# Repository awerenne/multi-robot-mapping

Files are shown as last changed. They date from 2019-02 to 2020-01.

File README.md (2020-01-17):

# Multi-robot environment mapping 

The goal of this project was to construct two robots, able to map unknown environments as quickly as possible. The considered environments are exclusively composed of straight black lines on a white background, intersecting each other with right angles. The robots being only allowed to move along those black lines during the exploration phase.

The developed solution follows a master-slave architecture. Each robot (slave) follows a black line while keeping track of the travelled distance. Once an intersection detected, the robot stops and sends an information message to the master. The message contains the type of intersection encountered and the travelled distance since the previous intersection. This information is then used by a program (master), running locally on a computer, in order to update its internal representation of the environment (i.e. map). The next instruction (stop, straight, turn left or right, uturn) for the robot is then computed and send back to the rboto. This procedure is repeated until the environment is entirely explored.

<p align="center">
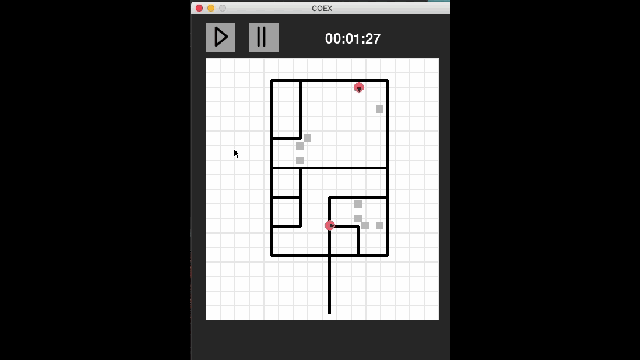
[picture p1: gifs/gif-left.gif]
    &nbsp;&nbsp;&nbsp;
    
</p>

The left-part of the animation above shows a live screen recording of the master constructing the map, corresponding to the robot exploration performed (displayed in the right-part). A video of the complete demonstration can be found [here](https://www.youtube.com/watch?v=w8zaz-Xr6bw&t=6s). The implementation and results are described in the [report](https://awerenne.github.io/files/pp-report.pdf). The different steps of the construction of the robots are documented [here](https://github.com/awerenne/multi-robot-mapping/blob/master/construction/README.md).

## Simulator
Testing the mapping algorithm with the exploration being performed by physical robots would have been time-consuming. Instead, the exploration was simulated on random environments. 

<p align="center">
    
</p>

The algorithm of the master is explained in the [report](report/personal-project.pdf)) (pages 8-11). A simulation can be lauched with <code>python main.py</code> in the folder *code/simulator/*. The flag <code>is_simulation</code> needs to be set to true in the config file.

## Robot
The control of the robot was tested with a simple challenge: following a curved line at a constant speed. To this end, a speed and steering controller were developed (described in the [report](report/personal-project.pdf), pages 20-24). The result is shown in the animation below.

<p align="center">
    
</p>

The robot was then further augmented to loop through a serie of steps during the exploration phase. The high-level view of the main algorithm (serie of steps) is implemented in the file *code/robot/mapping/mapping.ino*, which is based on low-level features implemented in the files located in the folder *code/robot/NewCOEX/*. The acronym COEX stands for cooperative explorer. 

<p align="center">
    
</p>

## Usage
The simulator can be launched as follows:
1. Set the flag <code>is_simulation</code> to True in the config file.
2. Run the command <code>python main.py</code> (in the folder *code/simulator/*).

The physical exploration can be launched as follows:
1. Copy the folder *code/robot/NewCoex* in your Arduino folder, and load it as a library ([how to load a library](https://www.arduino.cc/en/guide/libraries)).
2. Install the library corresponding to the [QTR-X sensors](https://www.pololu.com/docs/0J19/2).
3. Upload the program *code/robot/mapping/mapping.ino* to the micro-controller.
4. Set the flag <code>is_simulation</code> to False in the config file.
5. Check that the ports in the config files are correctly configured with the names of the bluetooth modules.
5. Switch the power of the robots on and calibrate the line sensors.
6. Run the command <code>python main.py</code> (in the folder *code/master/*).

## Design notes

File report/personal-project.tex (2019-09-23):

%\documentclass[12pt]{extarticle}
\documentclass[12pt]{report}
\usepackage[utf8]{inputenc}
\usepackage{cite}
\usepackage[hyperfootnotes=false]{hyperref}
\usepackage{xcolor}
\usepackage{tikz}
\usepackage{mathtools}
\hypersetup{
  colorlinks,
  citecolor=blue,
  linkcolor=red,
  urlcolor=blue}
\usepackage{amsmath}
\usepackage{subcaption}
\usepackage{amssymb}
\usepackage{graphicx}
\usepackage{float}
\usepackage{caption}
\usepackage{hyperref}
%\usepackage[linesnumbered,ruled,boxed,algo2e]{algorithm2e}
\usepackage{algorithm}
\usepackage{algpseudocode}
\usepackage{geometry}
%\usepackage{subfig}
\usepackage{bm}
%\geometry{left=30mm, right=30mm, top=30mm, bottom=30mm}
\geometry{
	paper=a4paper, % Change to letterpaper for US letter
	inner=3cm, % Inner margin
	outer=3.5cm, % Outer margin
	bindingoffset=.5cm, % Binding offset
	top=2.8cm, % Top margin
	bottom=2.8cm, % Bottom margin
	%showframe, % Uncomment to show how the type block is set on the page
}
%\usepackage{subfig}
%\usepackage{mwe} % For dummy images
%\usepackage{capt-of}
\usepackage{tabu}
\captionsetup{
	margin=1.2cm,
	format=hang,
	font=small,
	format=plain,
	labelfont={bf,up},
	textfont={it}}
%\setlength{\footskip}{15mm}
\renewcommand{\thesection}{\arabic{section}}
\parskip 1.5ex % paragraph spacing
%\renewcommand{\baselinestretch}{1.33} % line spacing
\begin{document}
\newcommand{\HRule}{\rule{\linewidth}{0.5mm}} % Defines a new command for the horizontal lines, change thickness here
 
%----------------------------------------------------------------------------------------
%	AUTHOR SECTION
%----------------------------------------------------------------------------------------

\begin{titlepage}
\begin{center}

%\vspace*{.06\textheight}
%{\scshape\LARGE \univname\par}\vspace{1.5cm} % University name
\textsc{\Large Personal Project}\\[0.4cm] % Thesis type

\vspace*{.06\textheight}
\begin{center}
\\[1.2cm] 
\end{center}

\HRule \\[0.4cm] % Horizontal line
{\huge \bfseries Unknown Environment Mapping with multiple robots\par}\vspace{0.4cm} % Thesis title
\HRule \\[1.2cm] % Horizontal line
 
\begin{minipage}[t]{0.4\textwidth}
\begin{flushleft} \large
\emph{Author:}\\
Aurélien \textsc{Werenne }
\end{flushleft}
\end{minipage}
\begin{minipage}[t]{0.4\textwidth}
\begin{flushright} \large
\emph{Advisor:} \\
Bernard \textsc{Boigelot}
\end{flushright}
\end{minipage}\\[2.4cm]

Montefiore Institute\\
Faculty of Applied Sciences\\
University of Liège\\
Liège, Belgium\\[4cm] 

%\begin{center}
%\includegraphics[scale=0.6]{figures/logo-uliege}\\[1.6cm] 
%\end{center}
{\large Academic Year 2018 - 2019}
 
\vfill
\end{center}
\end{titlepage}
\pagenumbering{roman}
\renewcommand{\abstractname}{Foreword}
\begin{abstract}
This work was performed in the context of the optional course \textit{Personal Project} at the University of Liege. The goal of the course is to design and develop a realistic interdisciplinary project from the conceptual to the operational phase. Moreover, the project must be chosen by the student, approved by the advisor and carried out remotely. 

The choice was made to construct two robots cooperating to explore and map an unknown environment rapidly.

To conclude, I would like to express my sincere gratitude to my advisor Prof. Bernard Boigelot at the University of Liège. The door to Prof. Boigelot office was always open whenever I ran into a trouble spot or had a question about my project. He consistently allowed this project to be my own work, but steered me in the right direction whenever he thought I needed it. Thank you.
\end{abstract}
\tableofcontents
\clearpage
\pagenumbering{arabic}
\chapter{Introduction}
%------------------------------------------------
\section{Motivation}
%------------------------------------------------
Constructing a map of environments using robots can be of great interest for rescue teams, especially for environments situated in war zones or affected by natural disasters. In those cases the rapidity component is of particular importance. In an attempt to increase the speed of the exploration process researchers investigated the use of multiple robots \cite{burgard, kurt}.

In this work we decided to develop a simple algorithm for a dual robotic system whose goal is to map an environment like the one shown in Figure \ref{fig:env}. The algorithm was then validated in a self-constructed simulator. Once the results became satisfying, the robots were constructed and tested on physical environments.

\begin{figure}[!h]
\vspace*{4mm}
\centering

\caption{Example of the structure of an environment. The robots start their exploration at the bottom edge. In the physical world, the scale is such that the smallest edge displayed above corresponds to 20 cm.}
\label{fig:env}
\end{figure}

%------------------------------------------------
\section{Problem Statement \& Hypothesis}
%------------------------------------------------
The environments considered are exclusively composed of straight paths\footnote{Also called \textit{edges} and \textit{roads} interchangeably in this work.} intersecting each other with right angles, where the paths are modelled by black lines on a white background (see Fig. \ref{fig:env}). The robots are only allowed to move along the black lines. Furthermore, each robot is equipped with sensors enabling it to i) distinguish the black line from the white background ii) detect and classify an intersection iii) detect the other robot if it is in a very close range.

%------------------------------------------------
\section{Proposed Solution}
%------------------------------------------------
The proposed solution is implemented in the form of a master-slave architecture, where the master will be running locally in a computer and the slaves correspond to the robots (see Figure \ref{fig:master-slave}). The robots move through the environment while incrementing a distance counter until an intersection is encountered. In this case, the robot stops and sends an information message to the master, containing the travelled distance and the type of encountered intersection. The master receives this information, and is used to further construct an internal representation of the map. Next, the master computes the direction the robot needs to move towards to. This instruction is then send to the robot. It is worth noticing that the robot stays at rest during the decision process of the master. The code for this work can be found at \href{https://github.com/Werenne/multi-agent-mapping}{this}\footnote{Url: \url{https://github.com/Werenne/multi-agent-mapping}} repository.

\begin{figure}[!h]
\centering

\caption{Master-slave architecture.}
\label{fig:master-slave}
\end{figure}

The next chapter describes the implementation of the master and simulator. Chapter \ref{chapter-construction} then details the construction/implementation of the physical robot. 

\chapter{Master}\label{chapter-master}

%------------------------------------------------
\section{Random environment generation}
%------------------------------------------------
The structure of the environments on which our system is tested (in the simulator and physical world) is generated randomly. The algorithm for this task had to be written from scratch since no existent one could be found. The procedure is composed of three sequential steps,
\begin{enumerate}
\item \textit{Initialization}: initialize the set of edges as shown in Figure \ref{fig:gener-a}.
\item \textit{Destruction}: remove randomly 80\%\footnote{Determined arbitrary by experimenting.} of the interior edges.
\item \textit{Fixing}: adds an edge randomly on nodes disconnected from the rest of the graph (relative to the \textit{root node}\footnote{The root node refers to the node at the bottom, and corresponds also to the starting point of the robots.}). This process is repeated until all remaining nodes can be accessed from the \textit{root node}.
\end{enumerate}

\begin{figure}[!h]
\centering
\begin{subfigure}{.3\textwidth}
  \centering
  
  \caption{Initialization}
  \label{fig:gener-a}
\end{subfigure}%
\begin{subfigure}{.3\textwidth}
  \centering
  
  \caption{Destruction}
\end{subfigure}
\begin{subfigure}{.3\textwidth}
  \centering
  
  \caption{Fixing}
\end{subfigure}
\caption{Resulting environments of three steps of the generation.}
\label{fig:gener}
\end{figure}

%------------------------------------------------
\section{Simulator}
%------------------------------------------------
It would be costly in time to design, debug and evaluate the performance of the master algorithm if ran in combination with the physical robots. Thus, a simulator was constructed emulating environment and robots. In particular, the simulated robots are constrained to follow edges in the environment, with their sensory inputs limited to a one-step lookahead in the front, left, and right directions. Each robot increments its distance and once they encounter an intersection, an information message is send to the master.

%------------------------------------------------
\section{Communication protocol}
%------------------------------------------------
Messages are of the following form: $<$\textit{identifier}, \textit{sequence number}, \textit{message}$>$. The \textit{message} part corresponds to \textit{information} (type intersection \& distance) if the sender is a robot, or to an \textit{instruction} if it comes from the master. The \textit{identifier} is used to enable the master to distinguish robots, but also to prevent communication between the robots. Lastly, the \textit{sequence number} permits to trigger a recovery mechanism for unreceived messages and to ignore redundant messages. Delimiters ($<$, $>$) are used to verify that the entire message is received.

%------------------------------------------------
\section{Graphical User Interface}
%------------------------------------------------
Simulations are visualized in a Graphical User Interface (GUI), which was made with the framework \texttt{PyGame}\footnote{More information about the \texttt{Pygame} can be found \href{www.pygame.org}{here}.}. The GUI enables us, on the one hand to visualize the internal map representation of the master, and on the other hand the groundtruth environment and robots (see Figure \ref{fig:gui}). In order to keep the simulations smooth, the master, simulator and GUI are executed as separate threads. Let us emphasize that the same GUI is used for the physical robot exploration, but obviously does not display the groundtruth since it is not known \textit{a priori}. 

\begin{figure}[!h]
\centering

\caption{A snapshot of the Graphical User Interface (grey lines correspond to the groundtruth, black lines to the current internal map representation, coloured circles to the robots).}
\label{fig:gui}
\end{figure}

%------------------------------------------------
\section{Architecture \& Decision Algorithm}
%------------------------------------------------
\subsection*{Architecture}
The architecture of the master is composed of three main classes: \texttt{map}, \texttt{messenger} and \texttt{master}. When a message is send by a robot, it is first received, parsed and checked by the \texttt{messenger}. The information is then passed to the \texttt{map}, which updates the internal representation of the environment and the corresponding robot pose (position and orientation). Finally, the \texttt{master} computes and sends the optimal direction that must be taken by the robot.

\subsection*{Decision Algorithm}
A robot arriving at an intersection sends an information, and waits for a response containing the new instruction. This instruction is determined by the decision algorithm of the master and is described in the next paragraph. Beforehand, the concept of \textit{frontier}, although commonly used, must be defined: a frontier is referred to as an intersection with at least one unexplored edge.

The decision algorithm distinguishes three cases when a robot arrives at an intersection. In the first case, the intersection is a frontier, and the new direction is simply chosen by applying the left-hand-rule on the unexplored edges. In the second case, the intersection is not a frontier and there are are no remaining frontiers in the current map. The master concludes that the exploration is completed and the robots are send back to their initial position (root note). In the last case the intersection is not a frontier, however, at least one frontier is still remaining elsewhere in the current map. The robot is then assigned to a frontier, which is the one with the minimum Manhattan distance to the current position of the robot. Once the frontier assigned, the master computes the path to take for the robot via the $\text{A}^*$ algorithm\footnote{The Dijkstra algorithm improved with the heuristic that a path to a goal is always greater or equal to the Manhattan distance to that goal. This permits to avoid unnecessary computations. This heuristic is valid since all the angles are right.}. The robot moves towards the assigned frontier following the determined path. However, the path is recomputed at each intersection since the explored environment expands, and thus new optimal paths could potentially appear.
 
Simulations showed that using two robots with the aforementioned algorithm increased the rapidity by 61\% compared to only using one robot. Although these results may seem sufficient, four problems were observed during the simulations. These problems are described below along with a proposed solution. 

\subsection*{Avoiding robot encounters}
Since rapidity is the main objective, caution must be taken to avoid robot encounters as much as possible. Indeed, the recovery process (described below) would lead to a loss of time. The method applied to avoid encounters is a masking of the neighbouring edges (infinite weights in $\text{A}^*$) in the map around the other robot during the decision algorithm. Two cases are further distinguished. First, if the other robot is on an intersection, the neighbourhood is defined as the set of edges directly connected to that intersection. Secondly, if the other robot is moving on an edge, the neighbourhood corresponds to the neighbourhood of the next intersection the other robot will encounter. 

\subsection*{Handling robot encounters}
Masking the neighbourhood will not guarantee to entirely avoid robot encounters. For example, two robots moving from opposite sides on an unexplored edge cannot be predicted. If such an encounter occurs, one of the two robots is send out of reach, such that the second robot ucan compute a new path and move forward.

\subsection*{Updating assigned frontiers}
During the time a robot moves towards its assigned frontier, the other robot could potentially have already explore it, coming from another side of the frontier. This issue is solved by checking for each newly explored frontier if it has been assigned.

\subsection*{Cooperative strategy}
An attempt is made to induce a cooperative behaviour. We suggest that the exploration may be more efficient if the robots are forced, to a certain degree, to explore separate distant regions. To do this, the cost function deciding which frontier to assign is adapted as follows:
\begin{equation}
\text{cost}(\text{frontier}) = D(\text{current}, \text{frontier}) - \lambda D(\text{frontier}, \text{other robot})
\end{equation}
where the function $D$ represents the manhattan distance between two points, and $\lambda$ is the importance parameter controlling the trade-off between the two terms. Thus, the first term implies to choose the most nearby frontier, whereas the second term induces the robot to chose the frontier which will be the most distant form the other robot.

Different values of $\lambda$ are tested, Figure \ref{fig:coop} shows the mean (mean on 20 explorations) elapsed time\footnote{The elapsed time rescaled by the covered length of the corresponding environment.} of the explorations. The optimal trade-off seems to be for $\lambda = 0.875$.
\begin{figure}[!h]
\centering

\caption{Mean elapsed time for different $\lambda$'s.}
\label{fig:coop}
\end{figure}

%------------------------------------------------
%------------------------------------------------
%------------------------------------------------
%\part{Robot}
%------------------------------------------------
%------------------------------------------------
%------------------------------------------------

\chapter{Robot}\label{chapter-construction}
The first part of this chapter (Section \ref{sec:components} and \ref{sec:phys-constru}) discusses the physical aspects of the robot , id est its components and how these are assembled. The second part then describes the software and control aspect.

%------------------------------------------------
\section{Components \& Functions}\label{sec:components}
%------------------------------------------------
We identified seven different requirements the robots needs to fulfil. They must be able to 
\begin{itemize}
\item perform basic computations.
\item move and rotate.
\item localize black lines on white background.
\item avoid collisions with the other robot.
\item measure the travelled distance.
\item communicate with the master.
\item supply power to its components.
\end{itemize}

\subsection*{Computational unit}
The \texttt{Arduino Nano} is used as the micro-controller. The main advantages being its simplicity of use and relatively small dimensions. On the other hand, the \texttt{Arduino Nano} only contains 14 digital pins and 8 analog pins, where some capabilities (e.g. interrupt, PWM) are only available on a subset of these pins. As a consequence, the connectivity was a puzzle-work and the final result is shown in Figure \ref{fig:electric-diagram}.

\subsection*{Line localization}
Straightforwardly, in order to perform efficient line-following it is important to be able to localize the line with respect to the center of the robot. This is done using an infra-red (IR) reflectance sensor, composed of an infra-red transmitter and a photo-diode receptor. The idea being that the reflectivity of infra-red light varies with the color and distance of the reflecting surface. In particular, the transmitter emits an infra-red beam onto a surface, which reflects the beam back at the diode. For a light-coloured surface (e.g., white background), the intensity of the reflected signal will be high, resulting in a flow of current in the diode. On the contrary, if it is dark-coloured (e.g., black line), then the intensity of the reflected signal will be low, resulting in a blocking diode. Placing an array of those sensors side-by-side, enables the robot to localize the black line. 

Instead of constructing such an array from separate sensors, we use the \texttt{QTRX-MD-06A Reflectance Sensor Array}, consisting of six IR sensors (see Figure \ref{photo-bottom} in Appendix \ref{chap-construction}). In addition, it comes with high-level interface permitting the robot to directly obtain a continuous value for the position of the line (0 if line at left extremity, 5000 if line at right extremity), which is a significant advantage since it improves the smoothness of the control system (see Section \ref{sec:line-control}). 

From this value we will the \textit{error line} is computed, defined as the deviation from the center of the robot. Figure \ref{fig:exp-qtr-flow} shows the error for a manually moving black line. As can be seen, the measures do not contain significant noise, due to under-the-hood pre-processing steps of the \texttt{QTRX} sensor. Despite this, it was found experimentally that shadow differences in luminous environments could affect the performance. To solve this issue, a shield in carton was constructed and placed around the sensor (see Figure \ref{photo-bottom}).
\begin{figure}[!h]
\centering

\caption{Experiment where a black line is moved back-and-forth between the left and right side of the robot.}
\label{fig:exp-qtr-flow}
\end{figure}

\subsection*{Obstacle detection}
Since multiple robots are moving in the environment, collisions could occur. To avoid this, a \texttt{Sharp} sensor is placed in front of the robot to detect its peers. A Sharp sensor is also an infra-red sensor but with an additional feature, it measures the distance to an object and returns a corresponding analog value. In our use-case, the desired behaviour is to trigger a signal quickly for an object in a range close to collision. In order to do this, the \texttt{Sharp GP2Y0D805Z0F} was chosen, detecting objects in a range 0.5-5 cm interval, and has a very responsive detection time.

It is recommended to add a bypass capacitor because the sensor draws current in large and short bursts. A bypass capacitor is a low-pass filter placed across the power and ground close to the sensor, to diminish the possible interferences resulting from these bursts.

\subsection*{Moving}
The robot is designed as a differentially steered two-wheel. Differential in the sense that both wheels can have different rates of rotations but unlike a differential gearing system as in automobiles, a differentially steered system will have both wheels powered. In other words, to go to the left (resp. right) the speed of the right (resp. left) motor is increased. Additionally, a free rotating wheel is placed at the front of the robot to keep the body in balance. The wheels are powered by brushed DC gearmotors with a 150:1 ratio (see Figure \ref{photo-bottom} in Appendix \ref{chap-construction}), controlled by sending a special form a digital signal, namely a pulse width modulation (PWM). The higher the absolute value of the PWM, the faster the revolutions of the motor are (a negative PWM corresponding to rotations in the opposite direction). Lastly, a dual H-bridge \texttt{L298n} is used in order to decouple the power supply to the motors and the arduino. 

\subsection*{Distance Measurement}
The robot computes the travelled distance in incremental steps by multiplying speed and time, at short regular intervals. For this purpose, two quadrature encoders are soldered to the motors in order to measure the speed. The idea is that the rotating DC motors induce a hall effect in the encoders at each rotation. The used encoders trigger six counts per revolution. The number of revolutions of the left and right motor, are denoted respectively $n_L$ and $n_R$. The angular velocity of the left wheel can be computed as
\begin{equation}
w_L = 2\pi f_L
\qquad\text{with}\qquad	
f_L = \frac{n_L}{6\, G_b \, \Delta{t} }
\end{equation}
with $G_b$ the gearbox ratio, $f_L$ the rotation frequency and $\Delta{t}$ the elapsed time. The angular velocity of the right wheel is computed in an analogous manner. The robot being modelled as differentially steered two-wheel, we obtain the speed of the robot as
\begin{equation}
v = \frac{v_L + v_R}{2} = \frac{R(w_L + w_R)}{2}
\end{equation}

with $R$ the radius of each wheel. Thus, the travelled distance is written,
\begin{align*}
\Delta{x} &= v\Delta{t}\\
&= \frac{\pi R}{6 G_b}(n_L + n_R)
\end{align*}
Several factors are not taken into account in this computation such as acceleration, noise in the measurements and the fact that the robot experiences small deviations during the line-following process. With this in mind, the computed distance is discretized in sufficiently large intervals (5 cm) to be considered an entirely error-free measure of the travelled edge length's. Since the counts of the encoders must occur independently of the program flow, interrupt routines were used.

\subsection*{Communication}
Communication with the master is performed via a bluetooth module \texttt{HC-06}, which is adapted for establishing short range wireless data communication between two systems. Notably, a voltage divider was added to the circuit because of the difference between the logic level voltage of the Arduino ($0-5$ Volt) and the bleutooth module ($0-3.3$ Volt) (see Figure \ref{fig:electric-diagram}):

\begin{align*} 
V_{arduino} &=  \frac{R_4}{R_3+R_4}V_{bleutooth} \\[0.4cm]
 &=  \frac{2.2}{3.2}V_{bleutooth}
\end{align*}

\subsection*{Power supply}
Most components have a low current consumption, and no high-performance speed was required. Thus, a rechargeable NiMH Battery of 7.2 Volts with a capacity of 900 mAh seemed sufficient.

%------------------------------------------------
\section{Physical construction}\label{sec:phys-constru}
%------------------------------------------------
The robot is constructed following the steps described below:
\begin{enumerate}
\item A chassis is cut from wood and used as a base. Additionally, four small pillars are pasted at the corners (see Figure \ref{photo-chassis} in Appendix \ref{chap-construction}).
\item The H-bridge is screwed on the chassis.
\item A breadboard is pasted on the pillars.
\item The micro-controller is soldered into header pins which are then fixed in the breadboard.
\item The encoders are soldered to the motors, and the latter are then fixed on the bottom of the chassis.
\item The wheels are placed on the shafts of the motors, and the omni-wheel is placed under the chassis, at the front.
\item The Sharp and QTR sensor along with its shields are fixed at their desired place.
\item Wiring all the components (see Figure \ref{fig:electric-diagram}).
\item Connect to the power via a soldered switch.
\end{enumerate}

\clearpage
\vfill
\begin{figure}[!h]
\centering

\caption{Electric diagram of the robot}
\label{fig:electric-diagram}
\end{figure}
\vfill
\clearpage

\section{High-level algorithm}\label{sec:high-algo}
The main steps of the robot's algorithm are detailed below. As can be observed, the robot executes mostly physical operations whereas the Master does all the 'smart' stuff.

\begin{algorithm}
    \caption{High-level view algorithm robot}
    \label{euclid}
    \begin{algorithmic}[1] % The number tells where the line numbering should start
    		\Procedure{main}{} 
    			\State active $\gets$ False
    			\State distance $\gets$ 0
			 \While{True}
			 	\If{\Call{checkMessage}{}}
					\State instruction $\gets$ \Call{readMessage}{}  
					\If{instruction $== 0$}
						\State \Call{stopMotors}{}
						\State active $\gets$ False
					\Else
						\State \Call{execInstruction}{instruction} \Comment{turn left, turn right, uturn}
						\State active $\gets$ True
					\EndIf
				\EndIf
				\If{active}
					\State \Call{followLine}{}
					\State distance $\gets$ \Call{measureDistance}{} + distance
					\If{\Call{isIntersection}{}} \Comment{see subsection below}
						\State type $\gets$ \Call{classifyIntersection}{} \Comment{see subsection below}
						\State \Call{forwardAlign}{} \Comment{see subsection below}
						\State \Call{send}{distance, type} \Comment{to Master}
						\State active $\gets$ False
					\EndIf
				\EndIf
				\State \Call{wait}{20} \Comment{milliseconds}
			 \EndWhile        		
        \EndProcedure
    \end{algorithmic}
\end{algorithm}

\subsection*{Intersection detection \& classification}
An anomaly is triggered when a black line is detected at one of the extremities of the \texttt{QTR} sensor. To distinguish noise, the robot continues its execution and checks if the same anomaly pattern occurs consecutively. If this is the case, the anomaly is finally viewed as an intersection. Whenever an intersection is detected, it continues its movement for a few inches in order to classify its type as given by Figure \ref{fig:types}.

\begin{figure}[!h]
\centering

\caption{Different types of intersections.)}
\label{fig:types}
\end{figure}

\subsection*{Forward align}
Since the robot rotates around its central point between the wheels, the robot first aligns the wheels with the detected intersection. This permits the robot to remain nicely aligned after a turn, and thus avoids large initial deviations in the line-following. In other words, once an intersection detected, the robot moves forward for a distance equivalent to its own length. As there may be no black line in front, the robot moves without the follow-line procedure, and instead controls the speed of the motors to be equal, in order to move in a straight line.

\section{Architecture}\label{sec:archi}
Figure \ref{fig:architecture} shows the architecture of the implementation in the micro-controller. The \textit{main} corresponds to the algorithm above. The \textit{COEX} class refers to the high-level features related to the cooperative exploration, which is based on low-level features. The advantages offered by this modularity are two-fold: it makes the debugging easier, and the low-level features can be re-used for a different purpose.

A particular problem observed experimentally was that the sensors and actuators obtained optimal performance levels at different frequencies. The implementation assigns a frequency object to each component to solve this issue.

\begin{figure}[!h]
\centering

\caption{Architecture of the code of the robot.}
\label{fig:architecture}
\end{figure}

%------------------------------------------------
\section{Control}
%------------------------------------------------
\subsection*{Line Following \& Speed Control}\label{sec:line-control}
As an amateur roboticist I naively thought that the robot would go straight if the signals (PWM) send to the left and right motor were equal. Figure \ref{fig:probs-control} shows the result of an experiment were the same PWM signal is send to both motors and their respective speeds are measured with the encoders. A varying difference between the two motors can clearly be noted. Moreover, we also observe that this relationship varies as the power supply discharges. With this in  mind a speed controller was developed in addition to a line-following controller. The two controllers take the form of a PID (with anti-windup) and are combined as shown in Figure \ref{fig:control-base}. Straightforwardly, the error of the speed controller is the \textit{target speed}\footnote{For the demo we fix the target speed to 8 centimeter per second.} $v^*$ minus the \textit{measured speed} $v$. On the other hand, the error of the direction controller is given by the so-called \textit{error line}, $x^*-x$ (previously discussed in Section \ref{sec:components}). The computed PWM values are denoted $u_L$ and $u_R$ for the left and right motor.
\begin{figure}[!h]
  \centering
  
\caption{Variations of speed between the motors}
\label{fig:probs-control}
\end{figure}

The tuning of the parameters of the speed controller is done with respect to a target speed varying as in Figure \ref{fig:tuning}. Notice that the measured speed in this Figure is the one obtained using the tuned parameters. The speed controller seems to work but there is still some room for improvements. However, the results were sufficient for our purpose and thus no further tuning was applied. 
\begin{figure}[!h]
\centering
\begin{subfigure}{.5\textwidth}
  \centering
  
  \caption{multiple cycles}
\end{subfigure}%
\begin{subfigure}{.5\textwidth}
  \centering
  
  \caption{average trend with bandwith representing the variance}
\end{subfigure}
\caption{Experiment speed control with a varying target speed}
\label{fig:tuning}
\end{figure}

To adjust the parameters of the direction controller, the robot was placed on a parcours formed by curved black lines. The heuristic used for tuning was to double the $K_p$ parameter until oscillations occurred, then half it back one time and start to tune the other parameters. Once this was done, the target speed was increased by a small increment and the process repeated (until the desired behaviour). 

By experimenting, several improvements were developed as can be viewed in the block diagram of Figure \ref{fig:control-base}. Indeed, the first observation to make is that there are a lot starts/stops during the exploration, which causes instabilities. It was suspected that this was due to a high current drainage by the motors for a sudden acceleration. The proposed solution implements a smoother acceleration profile\footnote{See Appendix \ref{chap-extra}.}. For a desired target speed to attain in a specific time interval, an intermediate value is computed, namely the \textit{progress speed} The progress speed follows an acceleration in trapezoidal form, permitting the robots to perform a slower start. 

Another challenge is that there can be a misalignment between the black line and the center of the robot after a turn. As a result, a \textit{derivative kick}\footnote{A derivative kick refers to a very large derivative as a consequence of a significant error. As large corrections are undesired, a common approach is to derive the measurements instead (already our case by default since setpoint remains unchanged) and to fix initial derivation to zero.} can occur, which was solved by fixing the initial derivation to zero. A second consequence of the misalignment is that in combination with the smooth acceleration, the correction at start from the direction controller is potentially significantly large with respect to the correction of the speed controller. This issue was solved by having a dynamic setpoint weighting, such that the direction correction is weighted with an hyperbolic tangent function converging rapidly with time to unity. 

\subsection*{Turning}
The COEX-1 is modelled as a two-wheel robot (see figure below). By integrating the angular velocity under the assumption that $v_R = -v_L$, rotational displacement can be deduced
\begin{equation}\label{eq:theta-turn}
\theta(t) = \frac{2vt}{b} + \theta_0
\end{equation}
\begin{figure}[hbtp]
\centering

\caption{Rotation of COEX-1}
\label{fig:model-turn}
\end{figure}

In order to rotate in a specific direction, a naive approach was first tested: rotating at a given speed and duration to obtain the desired angle using Equation \ref{eq:theta-turn}. The results were not catastrophic, but a significant variance was observed, going from a few degrees to a few dozens. This is not acceptable as our goal is to have the center of the robot aligned as closely as possible to the black line. 

A second approach tested, was to use \texttt{QTR} sensors to detect when the line was in the middle and at that instant, to stop the robot. Notice that if the the robot needs to turn 180 degrees but if edges are at his sides (90 degrees), the robot will stop to soon. To this end, the robot was first rotated with an angle of 130 degrees (using the method of the previous paragraph) and then continued with the \texttt{QTR} solution until the robot is aligned. An improvement was observed, however, the robot always stopped a little too late due to drift of the wheels with the surface and a lack of response time from the sensors/actuators.

Ideally, the robot would decrease its rotation speed when approaching the line and sufficiently slow to stop and be aligned perfectly. The implemented solution uses a simple controller so that the speed is decreased with respect to the error line measured. The deceleration was triggered from the moment the black line was in the range of the sensor (i.e., at one of its extremities).

\newpage
\null
\vfill
\begin{figure}[!h]
\centering

\caption{Schematic diagram of the control system (with anti-windup).}
\label{fig:control-base}
\end{figure}
\vfill
\begin{figure}[!h]
\centering

\caption{Schematic diagram of the improved control system (with anti-windup).}
\label{fig:control-base}
\end{figure}
\clearpage
\newpage

%------------------------------------------------
%------------------------------------------------
%------------------------------------------------
%\part{Result}
%------------------------------------------------
%------------------------------------------------
%------------------------------------------------

\chapter{Conclusion}\label{conclusion}
The algorithm of the master that was developed in simulation, showed satisfying results. We verified an improvement from using two robots instead of one. In addition, a slight performance gain was illustrated by inducing a simple cooperative behaviour, enforcing the robots to explore distant regions to a certain degree.

Constructing and implementing the physical robot to be robust and fast was challenging. Nevertheless, an efficient error-free mapping system with one robot could be demonstrated.

Finally, two robots were used to map a physical environment. No entirely error-free solution was found as collisions could not always be avoided for certain angles and speeds.

%------------------------------------------------
%------------------------------------------------
\newpage
\appendix
\chapter{Smooth acceleration}\label{chap-extra}
The default acceleration profile is uniform (see Figure \ref{fig:a}). The update of the progress speed is as follows
\begin{align*}
&v_{n+1} \leftarrow v_n + A \, \Delta t_{n:n+1}\\
&\text{with}\,\ A = \frac{v_{target}}{T}
\end{align*}
For a smoother transition, the robot accelerates following the trapezoidal profile as in Fig.\ref{fig:b}. As we want the robot to achieve the target speed in the same amount of time $T$. This constraint is developed,
\begin{align*}
&\Leftrightarrow \int_{0}^{T}a(t) =  \int_{0}^{T}a'(t) \\
&\Leftrightarrow A\,T = \underbrace{d\,B}_{triangles} + \underbrace{(T - 2d)B}_{rectangle}
\end{align*}
\begin{figure}[!h]
\centering
\begin{subfigure}{.5\textwidth}
  \centering
  
  \caption{uniform}
  \label{fig:a}
\end{subfigure}%
\begin{subfigure}{.5\textwidth}
  \centering
  
  \caption{trapezoidal}
  \label{fig:b}
\end{subfigure}
\caption{Acceleration profiles.}
\label{fig:ab}
\end{figure}
By substituting the parameter $\psi = \frac{d}{T}$, we obtain
$$
\boxed{B = \frac{A}{1-\psi}} 
$$
The update rule for the progress speed becomes
$$
v_{n+1} \leftarrow v_n + \int_{n}^{n+1}a'(t) = v_n + \int_{0}^{n+1}a'(t) - \int_{0}^{n}a'(t)
$$
Notice that with the right hand side of the above expression, we can make use of precomputed values of the geometric surfaces.
\chapter{Construction}\label{chap-construction}

\begin{figure}[hbtp]
\centering
\hspace*{-1.8cm}\begin{tikzpicture}
	\node [anchor=west] (bluetooth) at (-1.95,5) {\small Bluetooth};
	\node [anchor=west] (nano) at (-1.6,3) {\small Nano};
	\node [anchor=west] (sharp) at (-1.6,1) {\small Sharp};
	\node[anchor=south west,inner sep=0] (image) at (0,0) {};
	\begin{scope}[x={(image.south east)},y={(image.north west)}]
		%\draw[help lines,xstep=.1,ystep=.1] (0,0) grid (1,1);
		\draw[yellow,ultra thick,rounded corners] (0.62,0.25) rectangle (0.72,0.40);
		\draw[yellow,ultra thick,rounded corners] (0.35,0.60) rectangle (0.45,0.83);
		\draw[yellow,ultra thick,rounded corners, rotate around={48:(0.55,0.50)}] (0.55,0.50) rectangle (0.65,0.70);
		\draw [-latex, ultra thick, yellow] (bluetooth) to[out=0, in=-120] (0.35,0.6);
		\draw [-latex, ultra thick, yellow] (nano) to[out=0, in=-120] (0.5,0.55);
		\draw [-latex, ultra thick, yellow] (sharp) to[out=0, in=-160] (0.62,0.32);
	\end{scope}
\end{tikzpicture}
\caption{Front view of robot}
\label{photo-top}
\end{figure}

\begin{figure}[hbtp]
\centering
\hspace*{-1.5cm}\begin{tikzpicture}
	\node [anchor=west] (battery) at (-1.6,5) {\small Battery};
	\node [anchor=west] (shield) at (-1.6,3) {\small Shield};
	\node[anchor=south west,inner sep=0] (image) at (0,0) {};
	\begin{scope}[x={(image.south east)},y={(image.north west)}]
		%\draw[help lines,xstep=.1,ystep=.1] (0,0) grid (1,1);
		\draw[yellow,ultra thick,rounded corners] (0.65,0.35) rectangle (0.75,0.62);
		\draw[yellow,ultra thick,rounded corners] (0.38,0.23) rectangle (0.55,0.35);
		\draw [-latex, ultra thick, yellow] (battery) to[out=0, in=120] (0.65,0.62);
		\draw [-latex, ultra thick, yellow] (shield) to[out=0, in=-120] (0.38,0.23);
	\end{scope}
\end{tikzpicture}
\caption{Side view of robot}
\label{photo-side}
\end{figure}

\begin{figure}[hbtp]
\centering
\hspace*{-2.6cm}\begin{tikzpicture}
	\node [anchor=west] (array) at (-3.5,5) {\small Reflectance array};
	\node [anchor=west] (motors) at (-1.6,3) {\small Motors};
	\node[anchor=south west,inner sep=0] (image) at (0,0) {};
	\begin{scope}[x={(image.south east)},y={(image.north west)}]
		%\draw[help lines,xstep=.1,ystep=.1] (0,0) grid (1,1);
		\draw[yellow,ultra thick,rounded corners] (0.47,0.5) rectangle (0.68,0.65);
		\draw[yellow,ultra thick,rounded corners] (0.38,0.11) rectangle (0.75,0.25);
		\draw [-latex, ultra thick, yellow] (array) to[out=0, in=120] (0.47,0.65);
		\draw [-latex, ultra thick, yellow] (motors) to[out=0, in=150] (0.55,0.25);
	\end{scope}
\end{tikzpicture}
\caption{Bottom view of robot}
\label{photo-bottom}
\end{figure}

\begin{figure}[hbtp]
\centering
\hspace*{0.85cm}
\caption{Wooden chassis}
\label{photo-chassis}
\end{figure}

%\chapter{Algorithms}
%...

%\chapter{Miscellaneous}
%...

%------------------------------------------------
%------------------------------------------------
\bibliographystyle{plain}
\bibliography{biblio}

\end{document}

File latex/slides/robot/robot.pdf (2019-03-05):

## COEX-1

Cooperative Explorer

Aurélien Werenne
Advisor: Prof. B. Boigelot

University of Liège

March 4, 2019

Aurélien Werenne (ULiège) | Cooperative Explorer | March 4, 2019 | 1 / 37

## Overview

1 | General
2 | Components
3 | Control
4 | Exploration & Mapping
5 | Code
Aurélien Werenne (ULiège) | Cooperative Explorer | March 4, 2019 | 2 / 37

## General

Objective

The goal of the robot is to map an unknown environment in a centralized multi-agent setting.

The main features of the robots are:

Following a black line
Computing the travelled distance
Detecting, classifying and handling intersections

Avoiding obstacles
Communicating with a central unit
Aurélien Werenne (ULiège) | Cooperative Explorer | March 4, 2019 | 3 / 37

## General

Material

Arduino Nano
Reflectance sensor array
Sharp sensor

Magnetic encoders
Pololu micro metal gearmotor L298 dual H-bridge
NiMH Battery 7.2V
HC-06 Bluetooth module

Aurélien Werenne (ULiège) | Cooperative Explorer | March 4, 2019 | 4 / 37

## General

Structure

Photos (2 per slides, 4-5 slides)

Aurélien Werenne (ULiège) | Cooperative Explorer | March 4, 2019 | 5 / 37

## General

Variables

List of variables used in equations with small explanations

Aurélien Werenne (ULiège) | Cooperative Explorer | March 4, 2019 | 6 / 37

## Components

Sharp sensor

Explain flow test. Conclusion.

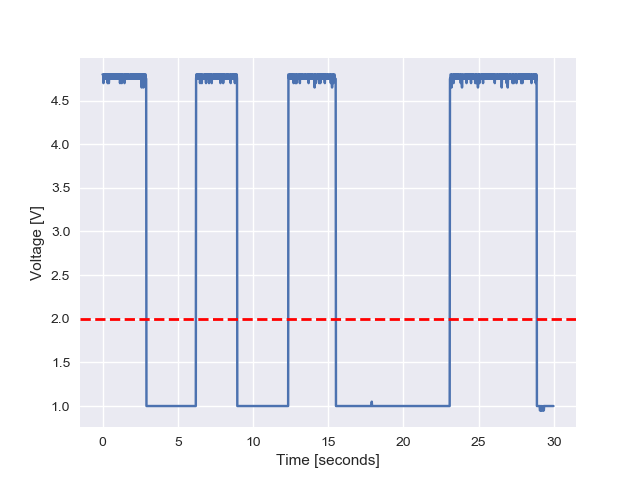
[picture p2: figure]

Figure: Obstacle movement (alternating between in and out of reach of sensor)

Aurélien Werenne (ULiège) | Cooperative Explorer | March 4, 2019 | 7 / 37

## Components

Reflectance sensor array (line sensor)

Explain flow test. Explain err line.

Plot.

Conclusion.

Aurélien Werenne (ULiège) | Cooperative Explorer | March 4, 2019 | 8 / 37

## Components

Shield

The line sensors are fixed vertically well above the given recommendations, such that the robot has place to climb hills. This decision made the line sensor particularly sensitive to ambient light interferences. Thus a shield had to be constructed.

Photo.

Aurélien Werenne (ULiège) | Cooperative Explorer | March 4, 2019 | 9 / 37

## Components

Bluetooth module (1/2)

Explain sender-receiver distortion.

Plots.

Conclusion.

Aurélien Werenne (ULiège) | Cooperative Explorer | March 4, 2019 | 10 / 37

## Components

Bluetooth module (2/2)

Logic level Arduino is 0 5 and HC 05 module is 0 3.3 V..

Varduino =

R2
R1 + R2

Vblt

=

2.2
3.2

Vblt

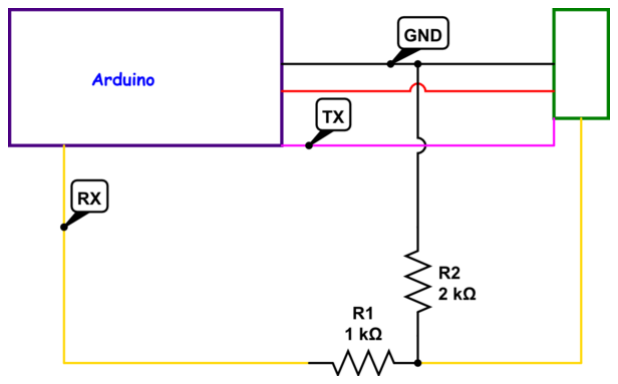
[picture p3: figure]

Figure: Voltage divider

Aurélien Werenne (ULiège) | Cooperative Explorer | March 4, 2019 | 11 / 37

## Components

Quadrature encoders (1/2)

wL = 2πfL | with | fL =

nL
N⁰ Gb ∆t

v =

vL + vR
2
| = | R(wL + wR)
| | 2
Aurélien Werenne (ULiège) | Cooperative Explorer | March 4, 2019 | 12 / 37

## Components

Quadrature encoders (2/2)

Remark why divide by 2 for counting. because only 2 pin interrupts.

Aurélien Werenne (ULiège) | Cooperative Explorer | March 4, 2019 | 13 / 37

## Components

Motors

Conclusion. Need for regulation. Two more curves on same plot but with full/empty battery.

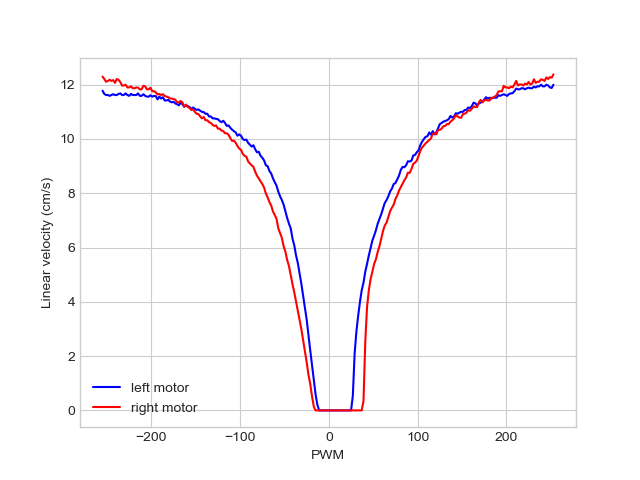
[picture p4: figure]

Figure: Relationship between PWM (input) and measured speed (output)

Aurélien Werenne (ULiège) | Cooperative Explorer | March 4, 2019 | 14 / 37

## Control

General framework

Use of classical PID controller.

on ← Kpen + Kd

en − en−1

∆tn−1:n

+ Ke

Xn

i=0

ei∆tn−1:n

with the following two precautions called respectively anti-windup and anti-derivative kick:

on =

max if on > max
min | if on < min
on | otherwise.
and | Kd =
0 | if n < T
Kd | otherwise.
Aurélien Werenne (ULiège) | Cooperative Explorer | March 4, 2019 | 15 / 37

## Control

Speed & direction

α = o(edirection)

β = o(espeed )

γ = o(ealign)

⇒

pwmL = (β − γ) + α
pwmR = (β − γ) − α
Aurélien Werenne (ULiège) | Cooperative Explorer | March 4, 2019 | 16 / 37

## Control

Line-following control

Recall plot of sensor.

edirection = errline ∈ [−2500; 2500]

Explain perturbation plot.

Perturbation plot.

Conclusion. break out angle. Agressive enough such that not seen as intersection.

Aurélien Werenne (ULiège) | Cooperative Explorer | March 4, 2019 | 17 / 37

## Control

Speed control (1/4)

Reason. Target and progress speed.

vn+1 ← vn + A ∆tn:n+1

⇔

Z T

0

a(t) = Z T

0

a

0
(t)

⇔ A T = d B
|{z}
triangles

+ (T − 2d)B
| | {z | }
| rectangle

We introduce the parameter ψ =

d
T

such that

B =

A
1 − ψ
Aurélien Werenne (ULiège) | Cooperative Explorer | March 4, 2019 | 18 / 37

## Control

Speed control(2/4)

vn+1 ← vn +

Z n+1

n

a

0
(t) = vn +

Z n+1

0

a

0
(t) −

Z n

0

a

0
(t)

Diagrams.

Aurélien Werenne (ULiège) | Cooperative Explorer | March 4, 2019 | 19 / 37

## Control

Speed control (3/4)

Reason.

Target and progress speed.

Equations.

Diagrams.

Aurélien Werenne (ULiège) | Cooperative Explorer | March 4, 2019 | 20 / 37

## Control

Speed control (4/4)

Explain plot.

PID plot.

Conclusion. Room for fine-tuning.

Aurélien Werenne (ULiège) | Cooperative Explorer | March 4, 2019 | 21 / 37

## Control

Forward

Explain forward. Explain improvement would be to consider theta instead.

edirection = vR − vL

We verify that if

vR;n > vL;n ⇒ en > 0 ⇒ αn > 0 ⇒ vR;n+1 ↑ , vL;n+1 ↓

Aurélien Werenne (ULiège) | Cooperative Explorer | March 4, 2019 | 22 / 37

## Control

Turning (1/2)

From Fig. we can easily deduce the model below by integrating the angular velocity .

θ(t) = 2vt
b
+ θ0 | because | vR = −vL

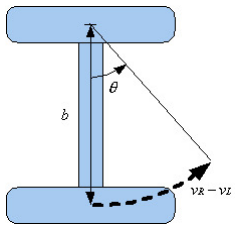
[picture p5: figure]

Aurélien Werenne (ULiège) | Cooperative Explorer | March 4, 2019 | 23 / 37

## Control

Turning (2/2)

θn+1 ←

2 vn ∆n:n+1
b
PID.
Aurélien Werenne (ULiège) | Cooperative Explorer | March 4, 2019 | 24 / 37

## Exploration & Mapping

General

To explore an unknown environment structured as a maze it needs to be able to:
Compute the distance travelled since the last intersection

Detect an intersection
Turn to the desired intersection
Aurélien Werenne (ULiège) | Cooperative Explorer | March 4, 2019 | 25 / 37

## Exploration & Mapping

Distance (1/5)

First method: Simple equation - explain without mathematics.

Second method: Upperbound of error can be reduced due to relation with distance.

plot relationship

Aurélien Werenne (ULiège) | Cooperative Explorer | March 4, 2019 | 26 / 37

## Exploration & Mapping

Distance (2/5)

Plot comparison with error bars of two methods on test set.

Conclusion.

Aurélien Werenne (ULiège) | Cooperative Explorer | March 4, 2019 | 27 / 37

## Exploration & Mapping

Distance (3/5)

Explain we could try to quantify uncertainty and above certain threshold not accept it.

MSE =

X

N

i=0

err ²
line

obtained iteratively by rolling mean method. One plot

Aurélien Werenne (ULiège) | Cooperative Explorer | March 4, 2019 | 28 / 37

## Exploration & Mapping

Distance (4/5)

Explain simpler choice is to discretize from second method discretization.

Remard 7.5-12.5 ....

Plot discretization on test set.

Aurélien Werenne (ULiège) | Cooperative Explorer | March 4, 2019 | 29 / 37

## Exploration & Mapping

Distance (5/5)

Example of resulting big map. Explain annotation

Map.

Aurélien Werenne (ULiège) | Cooperative Explorer | March 4, 2019 | 30 / 37

## Exploration & Mapping

Intersection detection

Explain problem of naive approach.

y = argmax
x∈{0,1}

mode(x)

Boolean value for intersection based on decision rule as follows

(yC = 0) ∨ (yL = 1) ∨ (yR = 1) ∨ (yF = 0)

Aurélien Werenne (ULiège) | Cooperative Explorer | March 4, 2019 | 31 / 37

## Exploration & Mapping

Intersection classification

Explain classification.

Figures of 8 types.

Aurélien Werenne (ULiège) | Cooperative Explorer | March 4, 2019 | 32 / 37

## Exploration & Mapping

Turning & alignment (1/2)

Problem with naive approach.

Solution + plot + equation.

Aurélien Werenne (ULiège) | Cooperative Explorer | March 4, 2019 | 33 / 37

## Exploration & Mapping

Turning & alignment (2/2)

Explain plot.

Plot to verify results.

Conclusion.

Aurélien Werenne (ULiège) | Cooperative Explorer | March 4, 2019 | 34 / 37

## Code

General architecture

Advantage.

Diagram.

Link to code.

Aurélien Werenne (ULiège) | Cooperative Explorer | March 4, 2019 | 35 / 37

## Code

Pseudo-code exploration

Pseudocode.

Aurélien Werenne (ULiège) | Cooperative Explorer | March 4, 2019 | 36 / 37

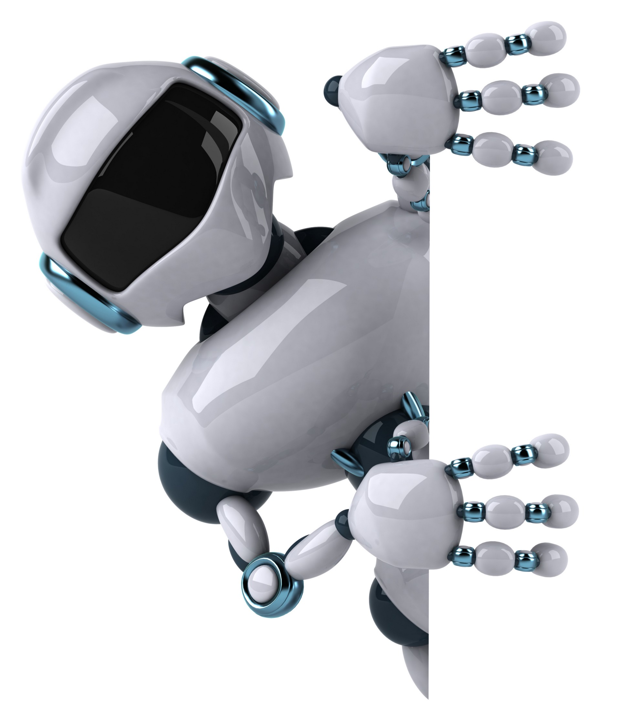
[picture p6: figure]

Aurélien Werenne (ULiège) | Cooperative Explorer | March 4, 2019 | 37 / 37

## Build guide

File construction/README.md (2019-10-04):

# Steps of construction #

1. A chassis is cut from wood and used as a base. Additionally, four small
pillars are pasted at the corners.

<p align="center">
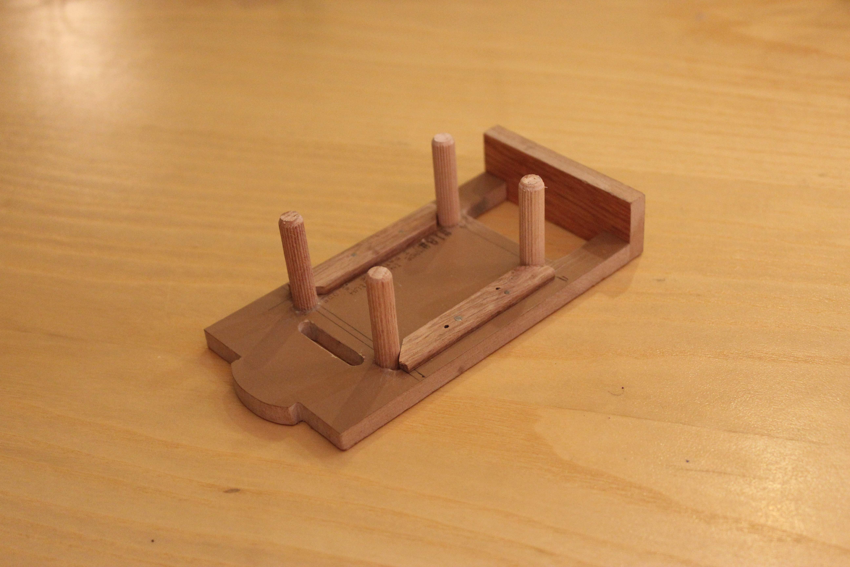
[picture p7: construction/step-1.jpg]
    
</p>

2. A breadboard is pasted on the pillars.

<p align="center">
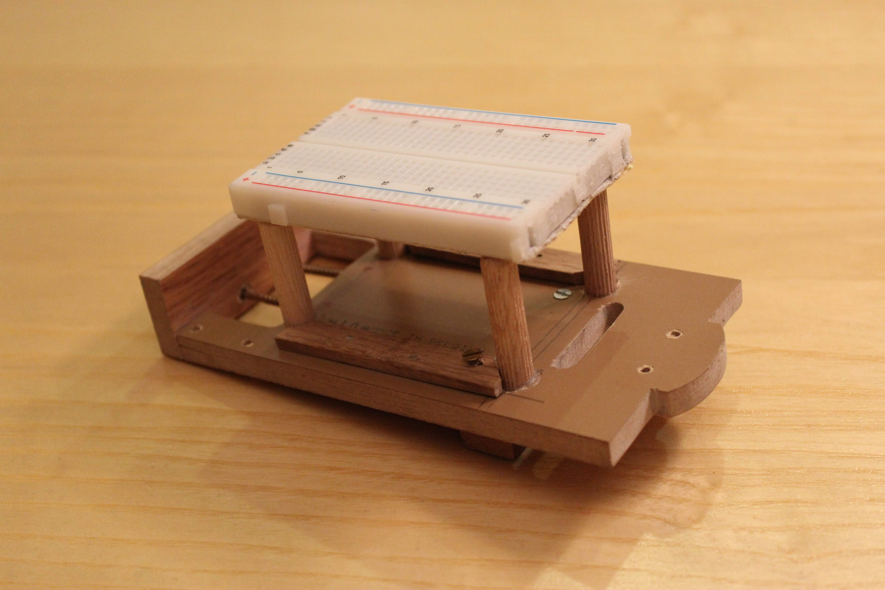
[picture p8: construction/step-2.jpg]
    
</p>

3. The H-bridge is screwed on the chassis.

<p align="center">
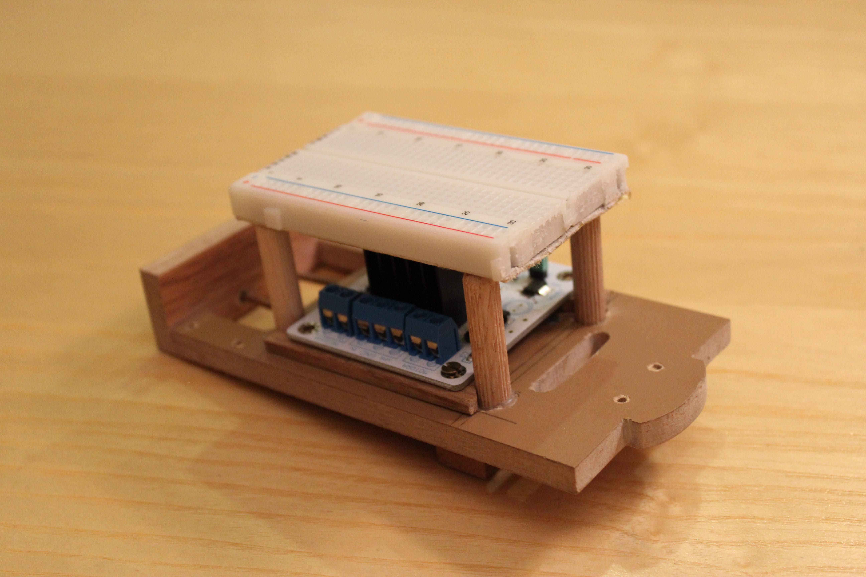
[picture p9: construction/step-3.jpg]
    
</p>

4. Solder encoders to the motors and header pins to the sensors.

<p align="center">
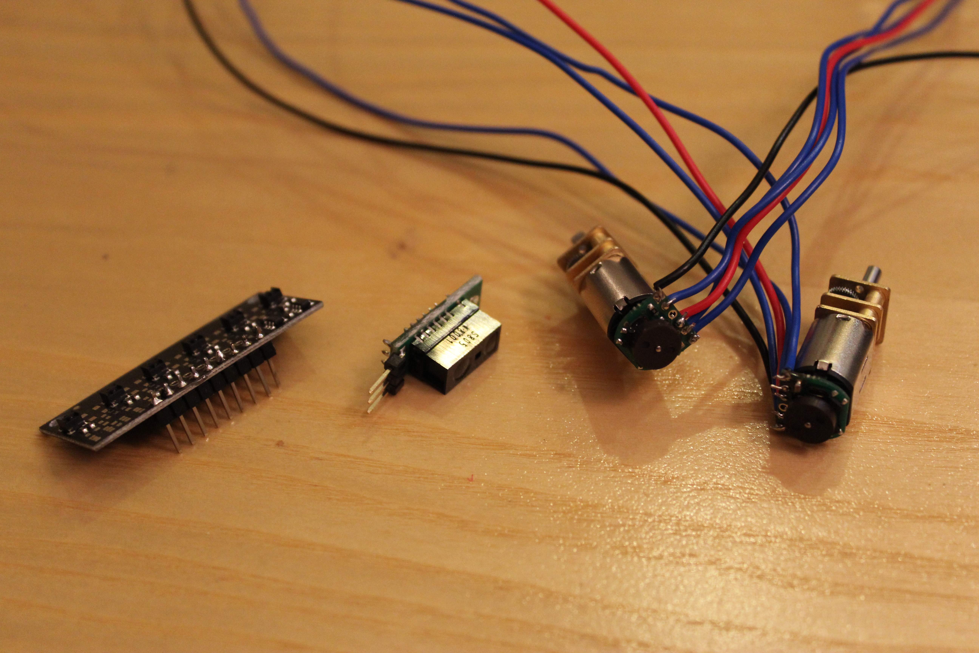
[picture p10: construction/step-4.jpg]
    
</p>

5. The micro-controller is soldered into header pins which are then fixed in the breadboard. The motors are fixed on the bottom of the 
chassis and the wheels are placed on the motor shafts.

<p align="center">
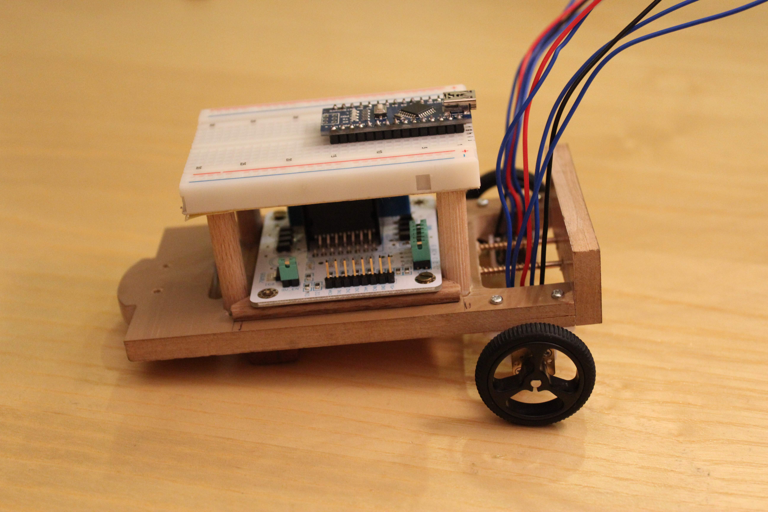
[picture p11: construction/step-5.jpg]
    
</p>

6. The omni-wheel is placed under the chassis, at the front.

<p align="center">
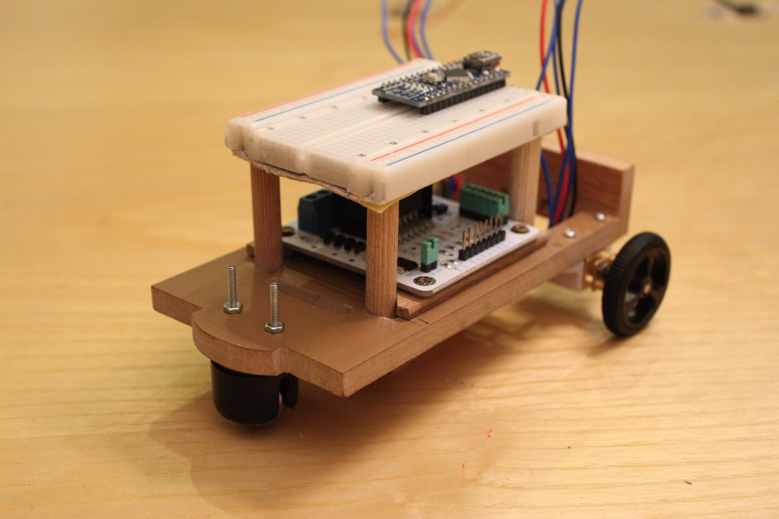
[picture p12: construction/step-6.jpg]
    
</p>

7. The QTRsensor along with its shields are fixed under the chassis.

<p align="center">
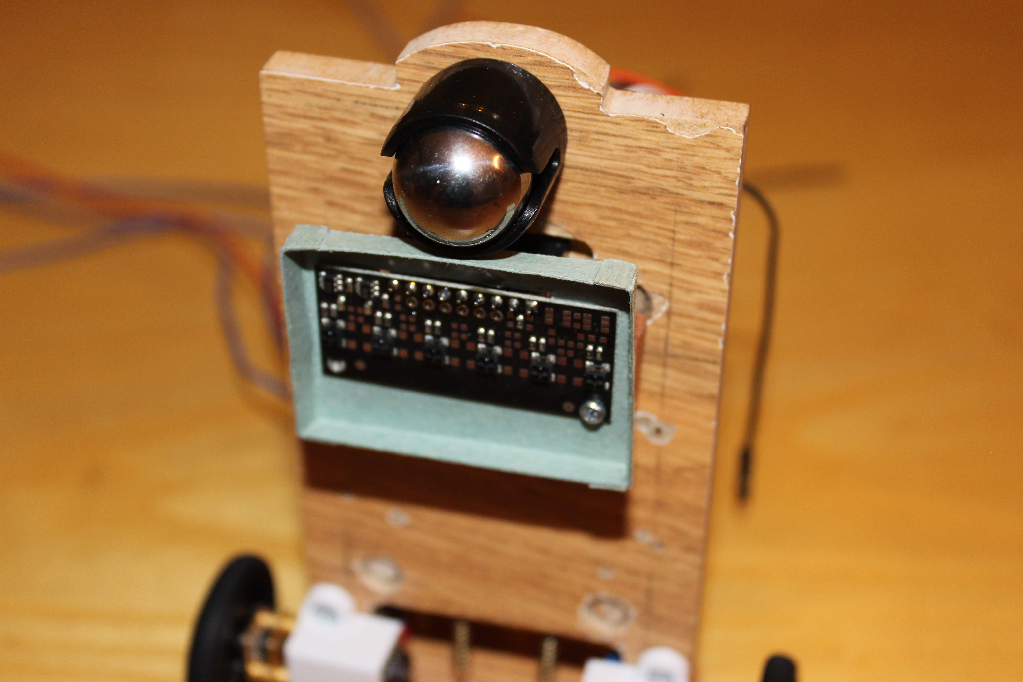
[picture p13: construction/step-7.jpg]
    
</p>

8. Wiring all the components as [here](../diagrams/electric.pdf).

<p align="center">
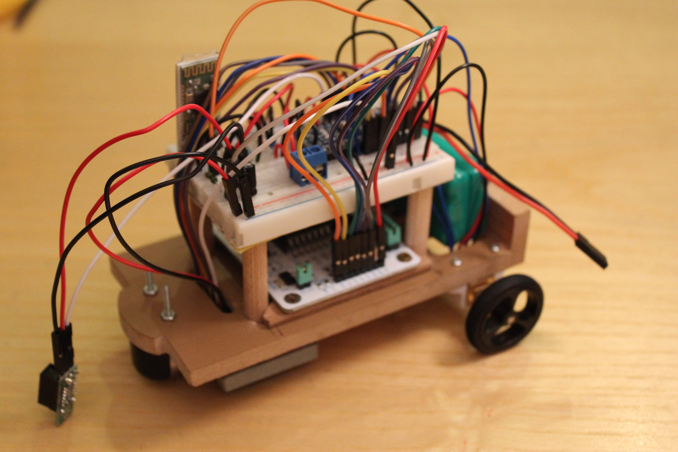
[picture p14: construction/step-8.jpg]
    
</p>

9. Solder swith.

<p align="center">
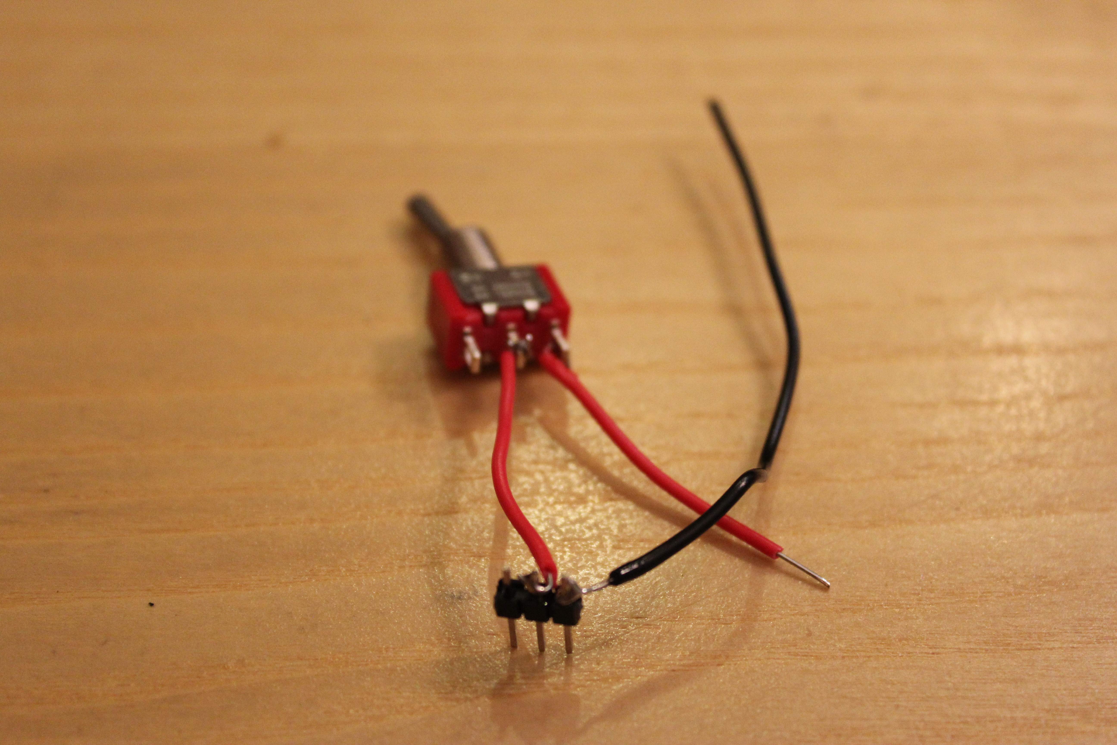
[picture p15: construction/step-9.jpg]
    
</p>

10. Connect the components to the power via the soldered switch. Paste the Sharp sensor on the chassis.

<p align="center">
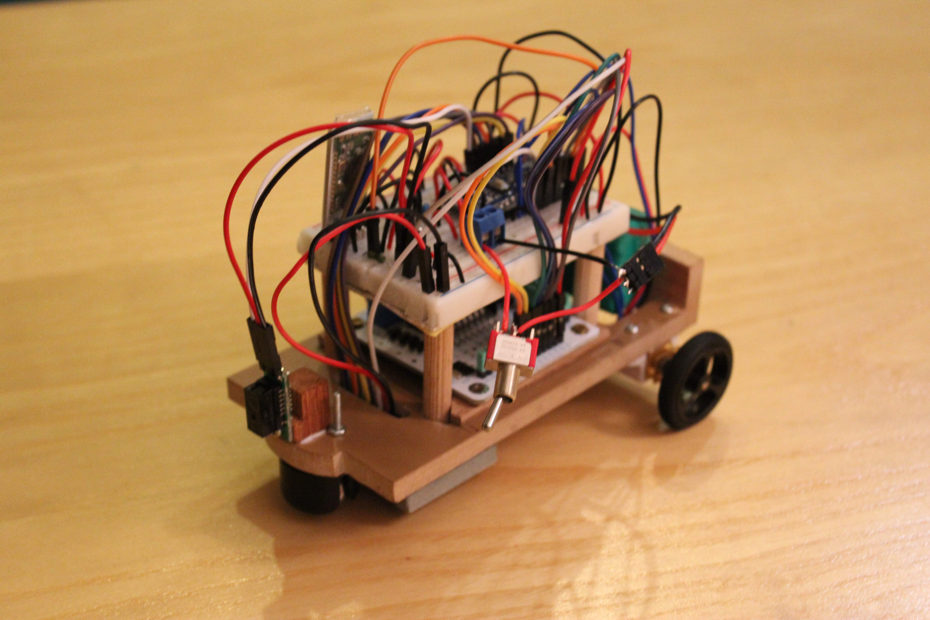
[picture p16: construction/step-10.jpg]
    
</p>

11. Make a second robot following the same steps.

<p align="center">
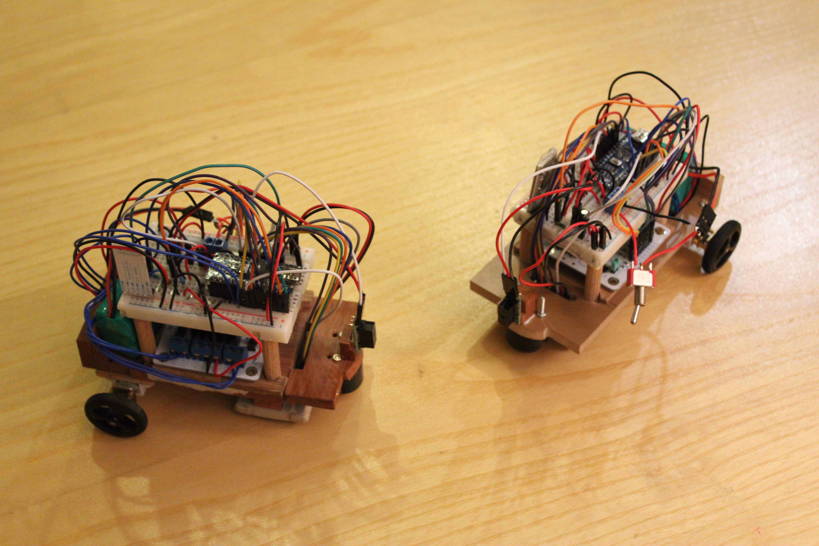
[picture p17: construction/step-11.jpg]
    
</p>

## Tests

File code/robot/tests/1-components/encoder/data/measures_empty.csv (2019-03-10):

pwm | speed_left | speed_right
-255 | -10.10 | -10.10
-253 | -10.12 | -10.12
-251 | -10.07 | -10.00
-249 | -10.07 | -9.93
-247 | -10.03 | -9.90
-245 | -10.05 | -9.91
-243 | -10.00 | -9.83
-241 | -9.96 | -9.79
-239 | -9.98 | -9.81
-237 | -9.96 | -9.72
-235 | -9.88 | -9.67
-233 | -9.94 | -9.74
-231 | -9.90 | -9.65
-229 | -9.86 | -9.65
-227 | -9.86 | -9.62
-225 | -9.87 | -9.67
-223 | -9.79 | -9.58
-221 | -9.83 | -9.55
-219 | -9.87 | -9.60
-217 | -9.79 | -9.48
-215 | -9.83 | -9.48
-213 | -9.79 | -9.45
-211 | -9.81 | -9.49
-209 | -9.67 | -9.40
-207 | -9.76 | -9.38
-205 | -9.74 | -9.42
-203 | -9.69 | -9.31
-201 | -9.62 | -9.31
-199 | -9.70 | -9.32
-197 | -9.62 | -9.27
-195 | -9.55 | -9.24
-193 | -9.55 | -9.24
-191 | -9.60 | -9.25
-189 | -9.48 | -9.17
-187 | -9.45 | -9.17
-185 | -9.49 | -9.18
-183 | -9.38 | -9.13
-181 | -9.38 | -9.06
-179 | -9.30 | -9.02
-177 | -9.35 | -9.08
-175 | -9.27 | -9.03
-173 | -9.27 | -8.96
-171 | -9.28 | -9.01
-169 | -9.20 | -8.93
-167 | -9.20 | -8.89
-165 | -9.21 | -8.90
-163 | -9.13 | -8.82
-161 | -9.17 | -8.75
-159 | -9.13 | -8.75
-157 | -9.18 | -8.80
-155 | -9.06 | -8.68
-153 | -9.06 | -8.68
-151 | -9.04 | -8.69
-149 | -8.99 | -8.54
-147 | -9.00 | -8.51
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

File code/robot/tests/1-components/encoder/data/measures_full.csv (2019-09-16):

pwm | speed_left | speed_right
-255 | -14.95 | -14.60
-253 | -14.99 | -14.64
-251 | -14.84 | -14.64
-249 | -14.84 | -14.57
-247 | -14.81 | -14.67
-245 | -14.85 | -14.92
-243 | -14.77 | -14.88
-241 | -14.74 | -14.84
-239 | -14.77 | -14.88
-237 | -14.70 | -14.84
-235 | -14.70 | -14.84
-233 | -14.74 | -14.92
-231 | -14.67 | -14.84
-229 | -14.60 | -14.84
-227 | -14.64 | -14.81
-225 | -14.64 | -14.85
-223 | -14.57 | -14.77
-221 | -14.53 | -14.70
-219 | -14.53 | -14.77
-217 | -14.50 | -14.70
-215 | -14.46 | -14.70
-213 | -14.46 | -14.67
-211 | -14.50 | -14.74
-209 | -14.39 | -14.67
-207 | -14.32 | -14.67
-205 | -14.43 | -14.67
-203 | -14.32 | -14.60
-201 | -14.29 | -14.57
-199 | -14.36 | -14.57
-197 | -14.18 | -14.57
-195 | -14.19 | -14.57
-193 | -14.22 | -14.53
-191 | -14.26 | -14.60
-189 | -14.15 | -14.50
-187 | -14.15 | -14.43
-185 | -14.19 | -14.53
-183 | -14.12 | -14.43
-181 | -14.08 | -14.39
-179 | -14.05 | -14.36
-177 | -14.05 | -14.36
-175 | -13.98 | -14.36
-173 | -13.98 | -14.32
-171 | -13.98 | -14.36
-169 | -13.94 | -14.25
-167 | -13.87 | -14.22
-165 | -13.91 | -14.29
-163 | -13.84 | -14.19
-161 | -13.80 | -14.12
-159 | -13.74 | -14.12
-157 | -13.80 | -14.19
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

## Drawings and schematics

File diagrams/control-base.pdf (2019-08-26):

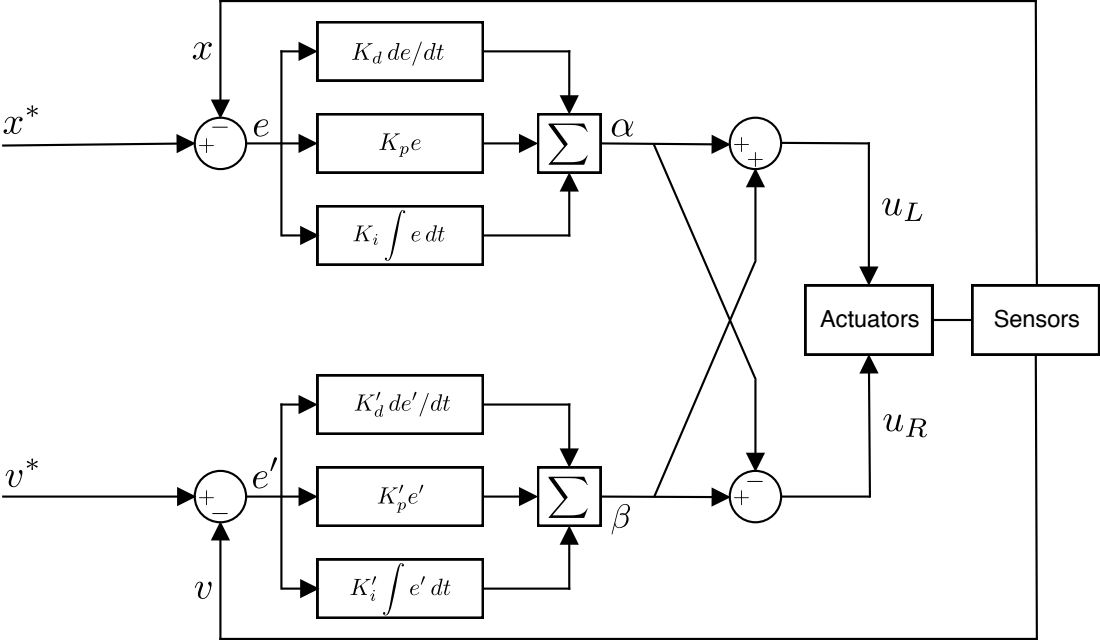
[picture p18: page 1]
Actuators; Sensors

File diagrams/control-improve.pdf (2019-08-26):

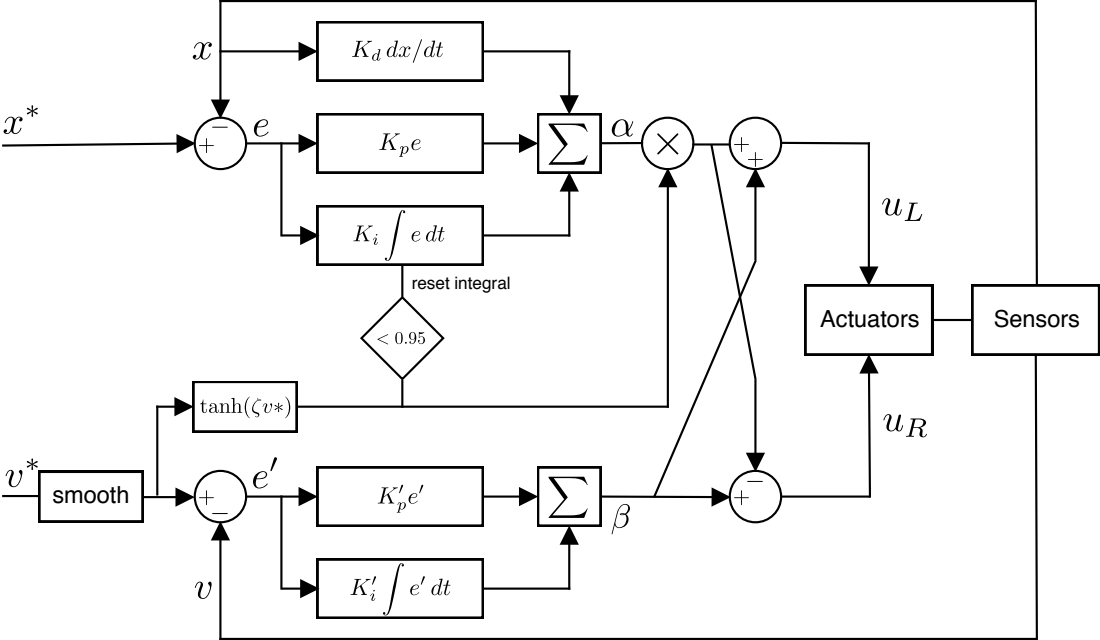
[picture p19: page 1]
Actuators; smooth; reset integral; Sensors

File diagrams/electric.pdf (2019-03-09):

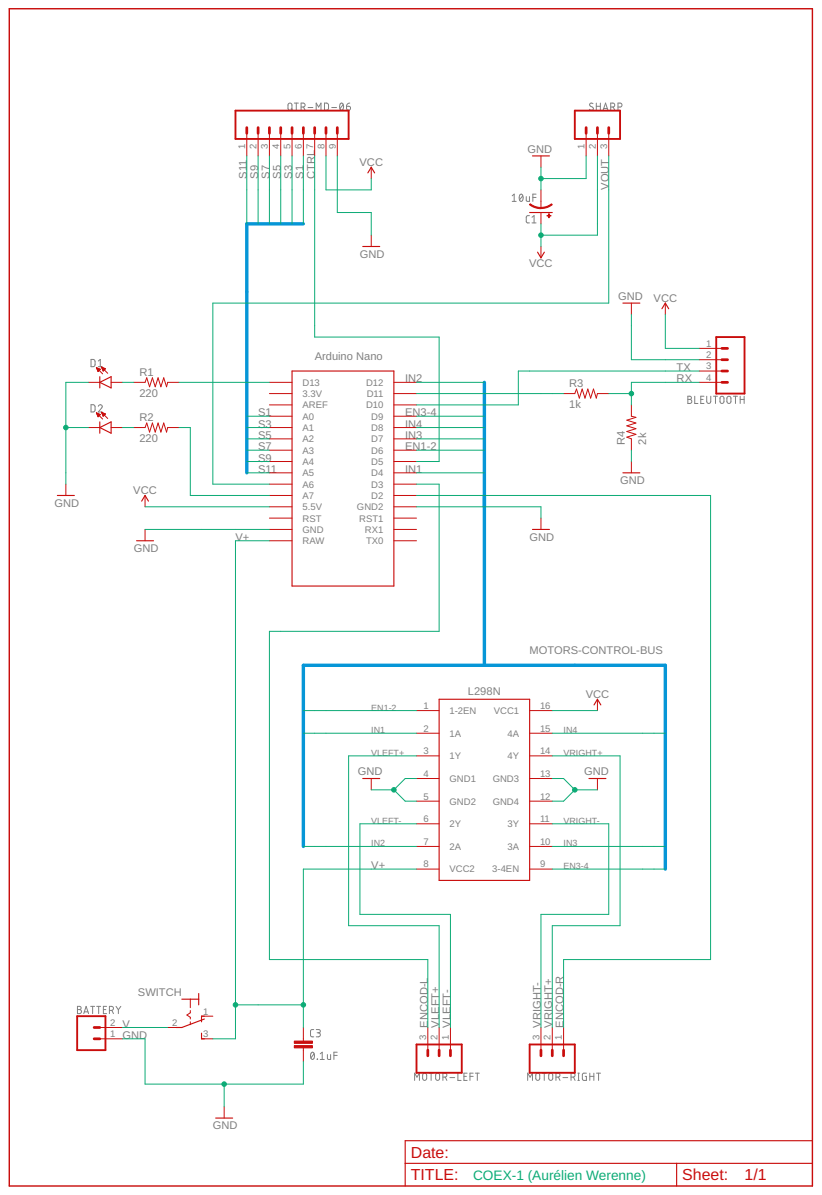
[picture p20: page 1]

EN3-4
IN4
IN3
EN1-2

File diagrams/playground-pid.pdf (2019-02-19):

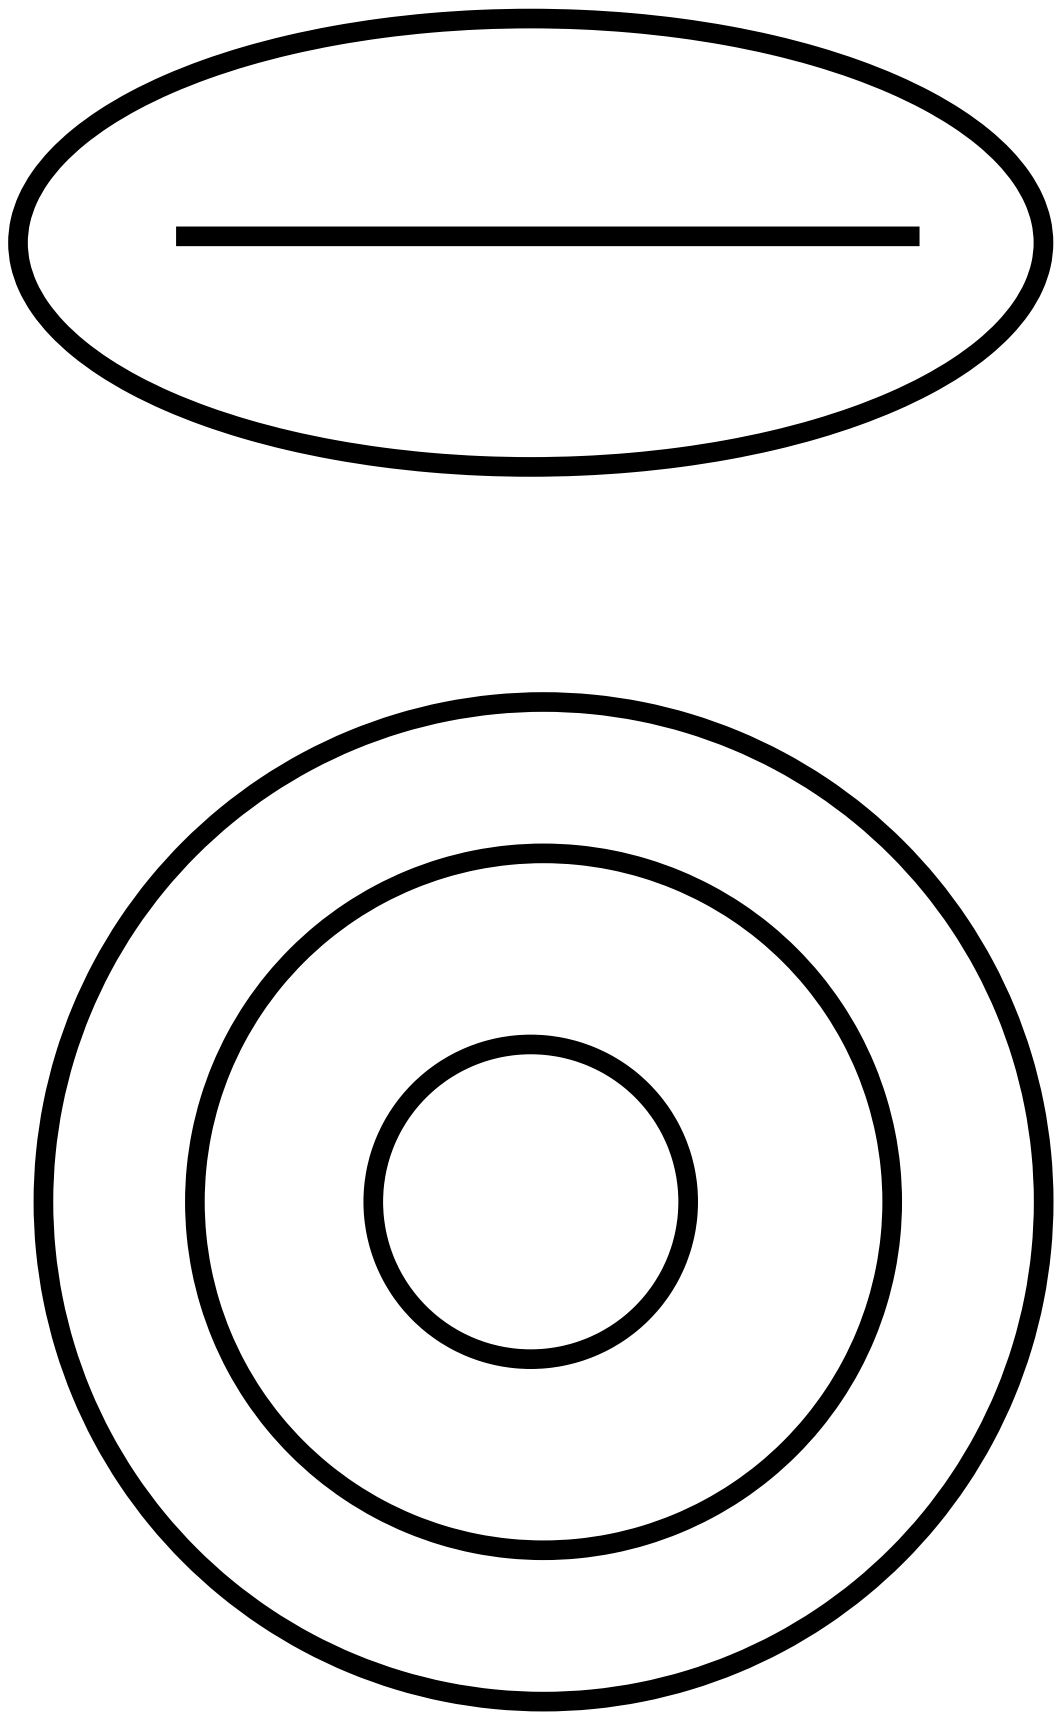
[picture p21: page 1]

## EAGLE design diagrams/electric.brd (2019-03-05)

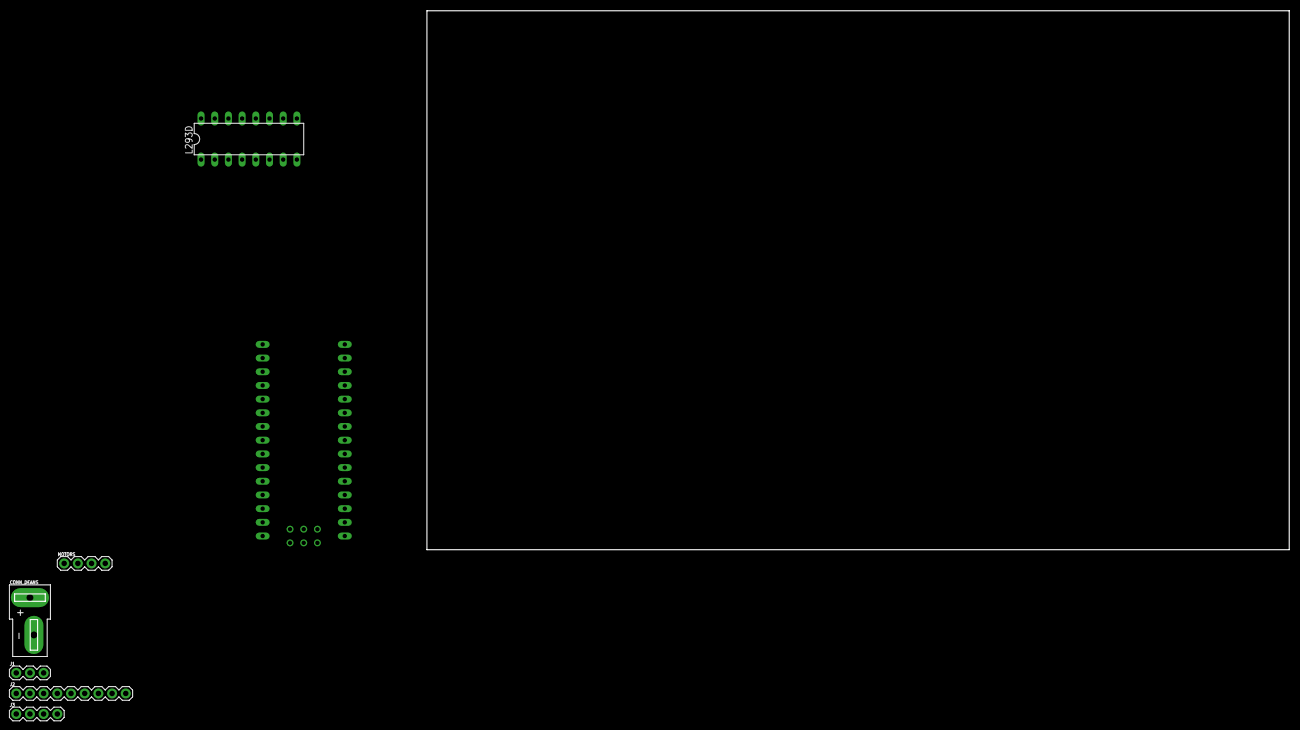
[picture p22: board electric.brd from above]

Board: 2 copper layers, 7 parts (0 on the bottom side), 7 nets, no tracks yet.

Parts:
CONN_DEANS: DEANS
J1: 1X03
J2: 1X09
J3: 1X04
L293D: L293D; DIL16
MOTORS: 1X04
U$1: NANO

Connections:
GND: CONN_DEANS.-, L293D.4, L293D.5, L293D.12, L293D.13, U$1.GND
GND-LEFT: L293D.6, MOTORS.3
GND-RIGHT: L293D.11, MOTORS.2
V+: CONN_DEANS.+, L293D.8, U$1.RAW
VCC: L293D.16, U$1.5V
VCC-LEFT: L293D.3, MOTORS.4
VCC-RIGHT: L293D.14, MOTORS.1

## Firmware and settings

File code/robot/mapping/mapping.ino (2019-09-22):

#include <Coex.h>

const byte pin_interrupt_left = 3;
const byte pin_interrupt_right = 2;
const byte pins_messenger[2] = {10, 11}; // RX, TX
const byte pins_actuators[6] = {4, 12, 6, 7, 8, 9};  // IN1, IN2, EN12, IN3, IN4, EN34
const byte pins_qta[6] = {A0, A1, A2, A3, A4, A5};  // Analog 
const byte pin_sharp = A6;
const byte led_signal = 13;
const int baud_rate = 9600;
const unsigned int pin_emitter = 5, n_sensors = 6, n_samples = 4;
const unsigned int parameters_qta[3] = {pin_emitter, n_sensors, n_samples}; 
Coex* coex = new Coex(pins_messenger, pins_actuators, pins_qta, pin_sharp,
            baud_rate, parameters_qta, 2);


//============
void setup() {
    pinMode(pin_interrupt_left, INPUT_PULLUP);
    attachInterrupt(digitalPinToInterrupt(pin_interrupt_left), update_counter_left, CHANGE);
    pinMode(pin_interrupt_right, INPUT_PULLUP);
    attachInterrupt(digitalPinToInterrupt(pin_interrupt_right), update_counter_right, CHANGE);

    Serial.begin(9600);
    while(!Serial) continue;
    flicker_led(led_signal, 10, 200);
    digitalWrite(led_signal, LOW);     
}


//============
void loop() {   
    digitalWrite(led_signal, HIGH);  
    //coex->automaticCalibration();
    coex->calibration();
    digitalWrite(led_signal, LOW);  
    delay(1000);
    float ret = 0, x = 8.5;
    while (true) {
        if(coex->availableMsg() && coex->readMsg() == 0)
            break;
    }
    int instruction = coex->getMsgInstruction();
    bool stopped = true;
    if (instruction != 1) exit(0);
    coex->newLine(8.5, true);
    while (true) {
        ret = coex->followLine();
        if (ret == -1) {
            coex->sendMsg(String(-1) + ";" + String(x));
            flicker_led(led_signal, 10, 1000);
            break;
        }
        if (ret == -2) {
            byte type_intersection = coex->typeIntersection();
            coex->sendMsg(String(type_intersection) + ";" + String(x));
            int instruction;
            //unsigned long init_time = millis();
            while (true) {
//                if (millis() > init_time + 3500) {
//                    coex->sendMsg(String(type_intersection) + ";" + String(-1));
//                    init_time = millis();
//                }
                if(coex->availableMsg() && coex->readMsg() == 0) {
                    instruction = coex->getMsgInstruction();
                    if (instruction != 0)
                        break;
                    else
                        coex->stop();
                }
            }
            
            switch (instruction) {
                case 0: coex->stop();
                        // exit(0);
                        break;
                case 2: coex->turnAlign(6.5, 0, coex->typeIntersection());
                        stopped = false;
                        break;
                case 3: coex->turnAlign(7.5, 1, coex->typeIntersection());
                        stopped = false;
                        break;
                case 4: coex->turnAlign(6, 2, coex->typeIntersection());
                        stopped = false;
                        break;
            }
            coex->newLine(8.5,true);
            x = -ret;
            x += 8.5;
        }
        x += ret;
    }
    exit(0);
}


//============
void flicker_led(byte led, unsigned int n, unsigned int delay_) {
    for (int i = 0; i < n; i++) {
        digitalWrite(led, LOW);
        delay(delay_);
        digitalWrite(led, HIGH);
        delay(delay_);
    }
}


//============
void update_counter_left() { coex->getSensors()->incrementLeft(); }
void update_counter_right() { coex->getSensors()->incrementRight(); }

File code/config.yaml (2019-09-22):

is_simulation: False
simulation:
    n_robots: 2
    robots: 
        1:  
            pose: [0,20,0]
        2:  
            pose: [0,0,0]
    dimensions: [800, 800]
    constants:
        WALL: 0
        FREE: 1
        OCCUPIED: 2       
real:
    n_robots: 2
    robots:     
        1: 
            pose: [0, 20, 0]
            port: "/dev/cu.HC-05-01-DevB"
            baud_rate: 9600
        2: 
            pose: [0, 0, 0]
            port: "/dev/cu.HC-05-DevB"
            baud_rate: 9600
    dimensions: [800, 800]
gui:
    dimensions_screen: [800, 800]
    dimensions_map: [600, 800]
    dimensions_user: [200, 800]
    frame_rate: 2
    colors:
        background: [255, 255, 255]
        free: [0, 0, 0]
        frontier: [192,192,192]
        robot_1: [255, 120, 120]
        robot_2: [120, 120, 255]
        direction: [0, 200, 100]
        user:
            background: [120, 120, 120]
            button: [120, 0, 0]
            font: [255, 255, 255]
    font:
        name: "couriernew"
        size: 35
    rect_run: [50, 120, 100, 50]
    rect_stop: [50, 200, 100, 50]
    width_line: 5
    width_frontier: 10
    radius_robot: 9
    title: "COEX"
helpers:
    map_orientation:
        'N': 0
        'E': 1
        'S': 2
        'W': 3
    map_type2edges:
        0: ['N', 'E', 'S', 'W']
        1: ['N', 'S', 'W']
        2: ['N', 'E', 'S']
        3: ['E', 'S', 'W']
        4: ['S', 'W']
        5: ['E', 'S']
        6: ['S']
        7: ['N']

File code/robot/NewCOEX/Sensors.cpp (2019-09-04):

#include "Sensors.h"


//============
Sensors::Sensors(const byte* pins_qta, const unsigned int* parameters,
        const byte& pin_sharp) {
    qtra = new QTRSensorsAnalog(pins_qta, parameters[1], parameters[2]);
    num_sensors = parameters[1];
    sensor_values = (unsigned int*) malloc(num_sensors * sizeof(unsigned int));
    this->pin_sharp = pin_sharp;
    pinMode(this->pin_sharp, INPUT);
    encoder_left = new EncoderState();
    encoder_right = new EncoderState();
}


//============
void Sensors::manualCalibration() {
    for (int i = 0; i < 400; i++) qtra->calibrate();  
}


//============
void Sensors::automaticCalibration(Actuators* actuators) {
    int clockwise = -1;
    int pwm_left = 85, pwm_right = 85;
    bool first_loop = true;
    for (int i = 0; i < 200;) {
        actuators->updatePWM(clockwise * pwm_left, -clockwise * pwm_right);
        if (first_loop) {
            for (int j = 0; j < 10; j++) qtra->calibrate();  
            i += 10;
        }
        else {
            for (int j = 0; j < 20; j++) qtra->calibrate();  
            i += 20;
        }
        actuators->stop();
        clockwise *= -1;
        first_loop = false;
        delay(200);
    }
    actuators->updatePWM(clockwise * pwm_left, -clockwise * pwm_right);
    for (int j = 0; j < 10; j++) qtra->calibrate(); 
    actuators->stop();
}



//============
void Sensors::oneStepCalibration() {
    qtra->calibrate(); 
}


//============
bool Sensors::ambientIsDark() {
    qtra->read(sensor_values, QTR_EMITTERS_OFF); 
    int min_value = 1000;
    for (int i = 0; i < num_sensors; i++) 
        if (sensor_values[i] < min_value) min_value = sensor_values[i];
    if (min_value >= 400) return true;
    return false;
}


//============
void Sensors::setCalibration(unsigned int* calib_min, unsigned int* calib_max) {
    qtra->calibratedMinimumOn = calib_min;
    qtra->calibratedMaximumOn = calib_max;
}      


// //============
// void Sensors::automaticCalibration() {
//     unsigned int calib_min_dark[6] = {100,100,100,100,100,100};  
//     unsigned int calib_max_dark[6] = {750,750,750,750,750,750}; 
//     unsigned int calib_min_light[6] = {100,100,100,100,100,100};  
//     unsigned int calib_max_light[6] = {600,600,600,600,600,600};  
//     if (ambientIsDark()) setCalibration(calib_min_dark, calib_max_dark);
//     else setCalibration(calib_min_light, calib_max_light);
// }


//============
void Sensors::qtraRead() {
    position = qtra->readLine(sensor_values);
}



//============
bool Sensors::isRoadLeft() {  
    return sensor_values[0] > 700;
    // return sensor_values[0] > 600;
}


//============
bool Sensors::isRoadRight() {  
    return sensor_values[num_sensors-1] > 650;
    // return sensor_values[num_sensors-1] > 600;
}


//============
bool Sensors::isRoadCenter() {  
    float sum = 0;
    for (int i = 1; i < num_sensors-1; i++) {
        sum = sensor_values[i];
        if (sensor_values[i] > 600) return true;
        // if (sensor_values[i] > 750 & getError() > -1850 & getError() < 1850) return true;
    }
    // if (sum > 1200)
    //     return true;
    return false;
}


//============
bool Sensors::isRoadFront() {  
    return (sensor_values[2] + sensor_values[3])/2 > 600;
}


//============
bool Sensors::isAligned() {  
    return false;
}


//============
int Sensors::getError() {
    /*
        Return x:
            x < 0 if line is left of center
            x > 0 if line is right of center
    */ 
    int center = (num_sensors-1)*1000/2;
    return (position-center);
}


//============
bool Sensors::isObstacle() {
    if (sharpVoltage() < 0.4) return true;
    return false;
}


//============
float Sensors::sharpVoltage() {
    int value = analogRead(pin_sharp);  
    return ((float) value)/1024.;       
}


//============
float Sensors::angularVelocity(const float& counts, const float& time) {
    /* 
        Radians per second
    */
    float gearbox_ration = 150.58, counts_per_revolution = 6;  
    float n_revolutions = counts / (gearbox_ration * counts_per_revolution);
    float frequency = n_revolutions / time * 1000;  // number of revol. per sec
    return 2. * 3.1415 * frequency;
}


//============
float Sensors::linearVelocity(const float& counts, const float& time) {
    /* 
        Centimeters per second
    */
    float radius_wheel = 0.8;  // cm
    return angularVelocity(counts, time) * radius_wheel;
}



//============
void Sensors::encodersReset() {
    encoder_left->reset();
    encoder_right->reset();
}


//============
void Sensors::incrementLeft() {
    encoder_left->incrementCounter();
}


//============
void Sensors::incrementRight() {
    encoder_right->incrementCounter();
}


//============
void Sensors::encodersRead() {
    encoder_left->newTimeStep();
    encoder_right->newTimeStep();
}


//============
float Sensors::getSpeed() { 
    float v_left = getSpeedLeft();
    float v_right = getSpeedRight();
    return (v_left + v_right)/2; 
}


//============
float Sensors::getSpeedLeft() { 
    float delta_counter = encoder_left->deltaCounter();
    float delta_time = encoder_left->deltaTime();
    return linearVelocity(delta_counter, delta_time);
}


//============
float Sensors::getSpeedRight() {  
    float delta_counter = encoder_right->deltaCounter();
    float delta_time = encoder_right->deltaTime();
    return linearVelocity(delta_counter, delta_time);
}


//============
float Sensors::getCounterDeltaTime() {
    return (encoder_left->deltaTime() + encoder_right->deltaTime())/2; 
}


//============
float Sensors::getDistance() {
    float v = getSpeed();
    float delta_t = getCounterDeltaTime();
    return 2 * v * delta_t / 1000; 
}

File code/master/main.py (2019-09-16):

from queue import Queue
from master import NaiveMaster
from gui import GUI
from utils import Parameters, Container
# from robots import Robots
# from environment import Environment

#---------------
def make_queues():
    q_master = {
        "master2gui": Queue(),
        "gui2master": Queue(),
        "robots2messenger": Queue(),
        "messenger2robots": Queue()
    }
    q_gui = {
        "master2gui": q_master["master2gui"],
        "gui2master": q_master["gui2master"]
    }
    q_robots = {
        "robots2messenger": q_master["robots2messenger"],
        "messenger2robots": q_master["messenger2robots"]
    }
    q = {
        "master": q_master,
        "robots": q_robots,
        "gui": q_gui
    } 
    return Container(q)

#---------------
if __name__ == '__main__':

    params = Parameters(path="../config.yaml")
    q = make_queues()
    # env = Environment().new()
    # robots = Robots(params, q.robots)
    master = NaiveMaster(params, q.master, lambda_=0.2)
    gui = GUI(params, q.gui, None)

    # Start child threads
    # robots.start()
    master.start()

    # Main thread
    while not gui.close:
        gui.check_user_event().update()

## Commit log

2018-10-30 Tests & bugs
    Adding of hardware tests. FIx bugs in simulator.
    [Actuators.cpp, Sensors.cpp, functions.ino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]
2018-11-26 Hardware tests & fix merge maps
    [Actuators.cpp, Sensors.cpp, functions.ino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]
2019-01-07 Test 1-9 & RobotInterface update
    [measures.csv, measures_test_2.csv, measures_test_3.csv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]
2019-01-10 Refactor structure of Master
    & Redo Map class
    [measures.csv, measures_test_2.csv, measures_test_3.csv]
2019-01-14 GUI with buttons
    + Automatic calibration
    + Mutually inclusive classes bug fixed
    + Intersection detection fixed
    [measures.csv, measures_test_2.csv, measures_test_3.csv]
2019-01-18 Multi-threaded architecture
    + finish test shortest path test
    + clean utils
    [Actuators.cpp, Sensors.cpp, config.yaml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]
2019-01-18 Improve distance approximation (include oneinch)
    + more robust intersection detection
    [measures_test_3.csv]
2019-01-21 Inheritance Master & Improved Graph structure
    + refactoring of map, graph
    [measures.csv]
2019-01-26 Master without bug (simulation & real world are working)
    [Actuators.cpp, Sensors.cpp, config.yaml]
2019-02-20 Refactoring tests
    Component tests done. Control tests in progress. Adding of Coex class (high level features of the robot)
    [measures.csv, measures_test_2.csv, measures_test_3.csv]
2019-02-21 Speed control and forward control (tests passed)
    PID with anti-windup
2019-02-22 Forward and turn control at constant speed
    Advanced tests qtr sensor, turn 90-180, frequencystate class, PID with init problem fixed
    [measures.csv]
2019-02-24 Acceleration with smooth option
    [measures.csv]
2019-03-05 Electric diagram + new tests
    [final.brd, final.sch, measures.csv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]
2019-03-09 Update schematic
    [final.sch]
2019-03-10 Update figs for slides
    [measures.csv, measures_empty.csv, measures_full.csv]
2019-03-10 Update Latex + Pid shaded plot + Sinus test plot
    [measures_test_2.csv, pid-speed.csv, reception-1hz.csv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]
2019-03-12 Perturbation test & PCB
    [perturbation.csv, pid-speed-old.csv, pid-speed.csv]
2019-03-13 Review slides & cleaner plots
    [measures_distance.csv, measures_test_3.csv]
2019-03-16 Update slides
    [measures_distance.csv, perturbation.csv]
2019-03-16 Zeta function + finish plots distance/perturbation
    [measures_distance.csv, perturbation.csv]
2019-03-17 Finished first version of slides
    [measures_distance.csv]
2019-03-17 Maze solving linked to master
    issue: bug for front detection
    [Coex.cpp, Sensors.cpp, config.yaml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]
2019-03-18 Maze mapping without bugs
    [Coex.cpp, Sensors.cpp, config.yaml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]
2019-03-20 Initial PCB sketch
    [pcb.brd, pcb.sch]
2019-06-19 Faster fluent motion
    [final.brd, final.sch, measures.csv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]
2019-06-25 Template grid diagram
    [electric.brd, electric.sch, pcb.brd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]
2019-08-28 Clean & Refactor
    [measures.csv, measures_distance.csv, measures_empty.csv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]
2019-09-04 Clean readme with animations & debug demo one-robot
    [measures.csv]
2019-09-16 Fix bluetooth bug when using two robots & update readme &
    [measures.csv, measures_full.csv, pid-speed.csv]

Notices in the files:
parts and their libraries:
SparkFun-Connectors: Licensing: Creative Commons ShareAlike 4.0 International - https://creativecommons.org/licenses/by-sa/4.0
